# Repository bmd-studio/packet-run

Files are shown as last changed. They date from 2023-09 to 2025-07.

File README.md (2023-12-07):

Packet Run
<br /> <br />
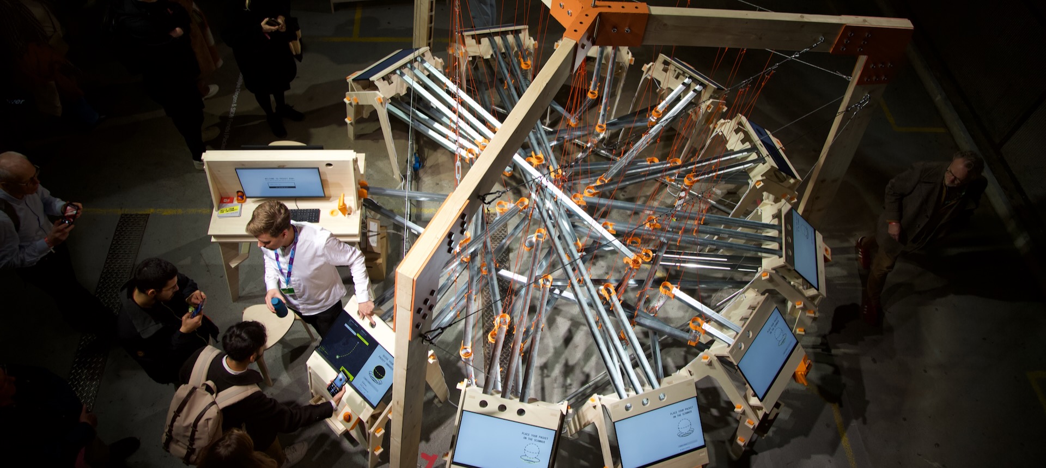
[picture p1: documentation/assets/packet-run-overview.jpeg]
Packet Run overview

<br />

Packet Run is an interactive art installation that visualises how data travels
across the internet in discrete packets. This process is known as **Internet
Protocol routing**.

Packet Run aims to clarify the hidden process of packet routing, thereby showing
everyday users what this process looks like, what risks are involved in the
process and what the future of the internet could look like.

Packet Run has been exhibited at the **2023 Dutch Design Week**,
October 21-29 2023. Afterwards, Packet Run is available for exhibition at
festivals, conferences and cultural institutions. 

For questions and inquiries, please get in touch with [Lei
Nelissen](https://leinelissen.com).

## Repository

This repository aims to contain all software, hardware, designs and other pieces
that are used to construct Packet Run and to make it tick. 

This repository is split out into a couple different directories that track
various assets, bits and pieces:
* `./client`: Contains all software that is run directly on the terminal units
* `./designs`: Contains various designs, ranging from logos, designed copy to
  STL files for the CNCed and 3D-printed parts of the installation. 
* `./documentation`: Contains documentation for how the installation is built,
  compiled and operated. Find here, for instance:
  * [The architectural diagram for Packet Run](./documentation/architecture.md)
  * [The project planning until the 2023 DDW](./documentation/planning.md)
* `./server`: Contains all software that is run on the server

## Contributors
Bureau Moeilijke Dingen

Packet Run was designed and built by **Bureau Moeilijke Dingen**, an Eindhoven-based
design studio that stimulates self-expression and autonomy through technology.

These people from Bureau Moeilijke Dingen contributed to Packet Run:
* Tijs Duel (3D Design, Mechanical Engineering)
* Jort Band (Technology, Management)
* Eva van der Born (UI/UX, Mechanical Engineering, Construction)
* Joep Elderman (Mechanical Engineering, Construction)
* Bart van Dijk (3D Design, Mechincal Engineering)
* Nils Hollestelle (Graphical Design, Construction)
* Lei Nelissen (Design, Project Management, Technology)

<br />

SIDN

Packet Run was based on [PathVis](https://github.com/SIDN/pathvis), an open
source tool that visualises traceroutes. PathVis was built by **SIDN Labs**, an
experimental group at the .NL domain registry focusing on experimental
technology at the core of the internet.

These people from SIDN Labs contributed to PathVis and Packet Run:
* Elmer Lastdrager
* Ralph Koning
* Caspar Schutijser
* Jelte Jansen

<br />

SIDN Fonds

Building Packet Run was made possible by a grant from **SIDN Fonds**, a public
fund that supports and strengthens the internet and its users. 

## Mentions & Media
After being exhibited at the 2023 Dutch Design Week, some media has picked up on
Packet Run. This is an (incomplete) collection of such mentions. Do note that
some (most) links are in Dutch.

- [Vint Cerf mentions Packet Run](https://elists.isoc.org/pipermail/internet-history/2023-November/009107.html)
- [Nemo Kennislink: Het internet als knikkerbaan](https://www.nemokennislink.nl/publicaties/het-internet-als-knikkerbaan/)
- [Studio 040: Opbouw Dutch Design Week in volle gang (video)](https://studio040.nl/nieuws/artikel/opbouw-dutch-design-week-in-volle-gang-ik-denk-dat-wij-voor-iedereen-hier-iets-te-bieden-hebben)
- [Telegraaf: Van dickpic booth tot volgelhuis uit riool...](https://www.telegraaf.nl/entertainment/804337822/van-dickpic-booth-tot-vogelhuis-uit-riool-waar-kijk-ik-naar-klinkt-massaal-tijdens-dutch-design-week)
- [SIDN: Packet Run is an interactive marble run...](https://www.sidn.nl/en/news-and-blogs/packet-run-is-an-interactive-marble-run-that-shows-people-how-the-internet-works)

## Video
Some recording were made at the Dtuch Design Week, so you can get an impression
of what Packet Run is like.

Packet Run Video on YouTube (https://www.youtube.com/watch?v=9uIs0sh4iYU)
<br />

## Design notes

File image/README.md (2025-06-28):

# Packet Run Image Generation

This directory contains the configuration and scripts for generating the Packet Run Raspberry Pi image using `rpi-image-gen`.

1. Install Podman (Desktop) if not already installed

## Building Images

### Client Image

To build the client image:

```bash
podman compose run build-client-image
```

### Server Image

To build the server image:

```bash
podman compose run build-server-image
```

The generated images will be available in the `deploy` directory.

## Configuration

### Layers

The image is built using layers defined in YAML files:

- `base.yaml`: Common setup including:
  - Node.js repository configuration
  - Tailscale repository configuration
  - Service templates
  - Base packages

- `client.yml`: Client-specific configuration:
  - Kiosk service setup
  - Hall sensor server setup
  - Client-specific packages

- `server.yml`: Server-specific configuration:
  - Server service setup
  - Server-specific packages

### Profile

The `packet-run-client` profile defines the order of layers to apply:
1. Base Debian system
2. Raspberry Pi specific layers
3. Packet Run base layer
4. Packet Run client layer

### Configuration File

The main configuration file `packet-run-client.cfg` includes:
- Base Debian configuration
- Profile selection
- Build options

## Development

To modify the image:
1. Edit the appropriate layer file in `config/meta/packet-run/`
2. Update the profile if adding new layers
3. Rebuild the image using the commands above

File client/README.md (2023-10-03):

# Packet Run — Client
This directory shall contain all software and documentation for running directly on terminal
units. Terminal units contain Raspberry Pi 4 boards.

## GPIO Pins
All terminals contain a [PN532-based NFC scanner board](https://www.tinytronics.nl/shop/nl/communicatie-en-signalen/draadloos/rfid/rfid-nfc-kit-pn532-met-s50-kaart-en-s50-key-tag). Some terminal units may
additionally contain a [3144 Hall Effect
sensor](https://www.tinytronics.nl/shop/nl/sensoren/magnetisch-veld/3144-hall-effect-switch).
Both pieces of electronics are to be connected to the Raspberry Pi GPIO pins, so
that the software can read them.

For reference on how the GPIO pins are numbered, use https://pinout.xyz.

### NFC Reader
The NFC scanner is read using WebSerial. This means that the board should be
connected as a UART device, so it is available over WebSerial. First of all,
make sure the DIP switches on the board are both set to OFF (towards the
numbers). This configures the PN532 in UART/HSU mode. When connecting the pins,
use the pin naming that is bound on the bottom of the board (GND/VCC/TXD/RXD).

The pins should be connected as such (board => RPI):
* GND => GND (pin 6)
* VCC => 5V (pin 4)
* SDA/TXD => UART 1 RX (pin 10)
* SCL/RXD => UART 1 TX (pin 8)

### Hall effect sensor
The hall effect sensor is read through a NodeJS webserver, the code for which
can be found in `./hall-sensor-server`.

Use a ribbon cable to connect the hall sensor to the Raspberry Pi. The following
pin layout connects the pins on the sensor from left to right when the side with
the serial number is facing you.

The pins should be connected as such (sensor => RPI):
* SUPPLY (left) => 5V (pin 2)
* GROUND (middle) => GND (pin 9)
* OUTPUT (right) => GPIO 2 (pin 3)

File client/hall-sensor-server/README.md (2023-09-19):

# Packet Run — Hall Sensor Server
This is a Node script that will output the value of a particular GPIO Pin (#2)
as a simple text-based API whether the magnet is engaged or not.

The API is server on `http://localhost:8000` and will output a simple `true` or
`false` for all routes. `true` means a magnet is close to the hall sensor,
`false` means a magnet is absent.

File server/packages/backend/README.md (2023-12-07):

# Packet Run — Back-end
This package contains the back-end code for Packet Run. It's a NestJS-based Node
back-end that is almost exclusively accessed through its GraphQL-based API,
powered by Apollo Server. It features a Worker Queue powered by BullMQ.

## Requirements
This package requires a relatively recent version of NodeJS (v20+
recommended). You will also need redis (v7+ recommended) for the event queue.

## Usage
1. In order to start the front-end, first install all NPM packages:
```
npm install
```

2. Then, create a `.env` file from the default example:
```
cp .env.example .env
```

3. (OPTIONAL) Set your [IPRegistry API
   Token](https://dashboard.ipregistry.co/keys) in the the `.env` file. If you
   don't set it, no IP metadata will be displayed.

4. Run all migrations
```
npm run initialize
```

5. Start the development server
```
npm run dev
```

The back-end is served by default on port `8080`. You may interact with it
through GraphQL (available on `http://localhost:8080/graphql`).

## Architecture
This codebase is split out into a number of modules, services and providers that
together create the full back-end service. You can find an overview of all
modules that are loaded in this application at `./src/app.module.ts`.

### Databasae
The back-end is powered by an SQLite database that is stored locally. By running
`npm run initialize`, this database is initialised, migrated and seeded. The
database is located in the `./data/packet-run.db` file.

The database is accessed through the MikroORM ORM layer. This layer features a
number of `entities` (or "models") that are stored in
`./src/entities/**/index.entity.ts`. Each files corresponds with a table in the
database, and the files contain the properties that should be available in the
database, along with their types.

The database is automagically migrated through the [MikroORM migration
manager](https://mikro-orm.io/docs/migrations). Whenever entity files are
changed, it's recommended to generate a new migration.

MikroORM also features subscribers, which allow create/update hooks for all
models. These are co-located with the entitities in `./src/entities/**/subscriber.ts`.

### GraphQL
The data is made available through an GraphQL API. In order to specify data
access for these, you can find resolvers (in `./src/entities/**/resolver.ts`)
that specify which models are available in the API and how they should exactly
be resolved. The output types for the GraphQL API are defined as GraphQL
"models" in `./src/entities/**/model.ts`.

These resolvers also specify which mutations should be made available to
clients, and how they should be handled. 

In order for the application to respond as quickly as possible to user inputs,
the back-end makes most of it data available across WebSockets, actively pushing
data to clients whenever models are updated. There is some glue code that hooks
into the MikroORM subscribers that automatically triggers GraphQL updates
whenever entities are changed.

### Jobs
We use traceroute to gather the route to a particular website. As traceroute is
asynchronous, we need to perform some tasks asychronously, as new addressed come
in. In order to facilitate this, we use a BullMQ queue, with jobs that are
defined in `./src/jobs`.

These jobs include traceroute itself, retrieving IP metadata from IPRegistry, as
well as retrieving the website and exporting it as an image so we display it
later. The latter task is accomplished in a headless Chrome instance powered by
Puppeteer.

As the BullMQ queue is powered by redis, you will need to have redis installed
locally. Note that the current back-end implementation assumes your redis client
is unauthenticated.

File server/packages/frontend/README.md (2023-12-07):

# Packet Run — Front-end
This package contains the front-end for Packet Run. It's a React-based frontend
powered by [NextJS](https://nextjs.org). It features Apollo for data fetching,
Styled Components for styling and mapbox-gl for map rendering.

## Requirements
This package requires a relatively recent version of NodeJS (v20+
recommended). 

## Usage
1. In order to start the front-end, first install all NPM packages:
```
npm install
```

2. Then, create a `.env` file from the default example:
```
cp .env.example .env
```

3. (OPTIONAL) Set your [Mapbox API
   Token](https://account.mapbox.com/access-tokens/) in the `.env` file. If you
   don't maps will not work

4. Start the development server
```
npm run dev
```

Follow the link provided in your CLI and the application should be work. This
codebase assumes the back-end will be running on the same host on port `8080`.
Please refer to the [back-end documentation](../backend/) for information on
setting up the back-end.

A dashboard is available on the root route (http://localhost:3000/) that
displays the back-end status for the full system.

## Architecture
This codebase is structured so that the Raspberry Pi clients connect to the
back-end through a URL that is formatted according to their id (e.g.
`http://localhost:3000/terminal/8`). Depending on the terminal type, they are redirected
to their respective pages (e.g. `http://localhost:3000/router/8`). These various
pages handle functionalities specific to their terminal type. 

In these pages, the front-end will make a connection to the back-end over
Websockets. Any time an update is issued, all data is updated and the page
re-renders. The philosophy for this codebase is that any and all changes are
send to the back-end, after which the back-end updates its data, updates are
sent over websocket the front-end and the front-end re-renders. As little data
is stored on-client as possible to mitigate risks of crashes.

The front-end attempts to connect to required peripherals, such as NFC readers
(connected via WebSerial) or Hall Sensors (connected over the [HTTP API hosted
by the client](../../../client/hall-sensor-server/)). The logic for these
connections is abstracted using the hooks in the `./src/lib` directory.

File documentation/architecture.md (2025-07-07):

# DDW2023 Software Architecture

## System diagram

```mermaid
flowchart LR
    subgraph server["Server (Raspberry Pi)"]
        subgraph workers["Workers"]
            hop-worker("Worker (mtr / traceroute)")
            website-worker("Worker (website)")
            ip-worker("Worker (IP Geolocate + WHOIS)")
        end

        frontend("Frontend (NextJS)")
        backend("NestJS (GraphQL)")
        websockets("Websockets")
        db("Database (SQLite)")
    end

    subgraph terminals["Terminals (Raspberry Pi x12)"]
        chromium("Interface (Chromium)")
        nfc-reader("NFC Reader (PN532)")
        config-server("Static Config Server (Caddy)")
        potentiometer("Potentiometer (optional)")
        pot-reader("Potentiometer reader script")
    end

    subgraph internal-routing["Internal Routing"]
        switch("Switch")
    end

    subgraph external-routing["External Routing"]
        internet("Internet (WiFi / Ethernet)")
    end

    internet <--HTTPS--> website-worker
    internet <--ICMP--> hop-worker
    internet <--HTTPS--> ip-worker
    internet <--WHOIS--> ip-worker

    backend <--IPC--> hop-worker
    backend <--IPC--> website-worker
    backend <--IPC--> website-worker
    backend <--IPC--> db
    backend <--IPC--> websockets

    frontend <--HTTP--> switch
    backend <--HTTP--> switch
    websockets <--WS--> switch

    switch <--HTTP--> chromium
    switch <--WS--> chromium
    chromium <--WebSerial--> nfc-reader
    config-server <--HTTP--> chromium
    config-server <--HTTP--> switch
    potentiometer <--"C(++)"--> pot-reader

    %% Could also connect to back-end instead, storing the state there and
    %% updating the terminal via a seperate WS connection
    pot-reader <--"WebMIDI / WS"--> chromium
```

## Table structure

### Relational

```mermaid

```

### Flat
```ts
/**
 * A single run tracks all data that is required for handling a succesful user
 * journey across the installation.
 */
interface Run {
    /** 
     * Uniquely identifies a full run. 
     * Format: nano-id, 12 characters (e.g. LtDWYYqPXujf) 
     */
    id: string;
    /** 
     * Format: 4- or 7-byte integer, hexadecimally encoded (e.g. 
     * `04 9C 64 D2 45 2B 80`).
     * NOTE: balls / NFC ID's MAY BE re-used, so there are no guarantees that 
     * an NFC ID uniquely identifies a particular request.
     */
    nfcId?: string;
    /**
     * The website the user has requested to route to.
     * Format: URL, including protocol, preferably HTTPS.
     */
    url: string;
    /**
     * The final destination (server) for this run.
     */
    destination: Address;
    /**
     * An ordered list that describes which hops are encountered en route to
     * the destination.
     * Format: array of `Address`es. null indicates that the hop is not responding
     * NOTE: The destination (server address) is NOT a part of the `hops` arrays
     */
    hops: (Address | null)[];
    /** 
     * At which terminal id this run was last seen
     * Format: number (terminal id)
     */
    terminalId: number;
    /** 
     * Describes the route that is taken during the run
     * Format: array of `Address`es and `Terminal`s
     */
    route: {
        address: Address;
        terminalId: number;
    }[];
}

/**
 * An interactive unit that can handle a number of tasks that are associated
 * with routing. Terminals are arranged in a circle, contain a screen, an NFC
 * reader and potentially a mechanism for creating/transforming packets.
 */
interface Terminal {
    /**
     * An unique identifier for a particular terminal. 
     * Format: 1-12 (potentially 1-20, including spares), with reserved numbers:
     * * 1: `sender`
     * * 2: `gateway`
     * * 3-4 + 6-8 + 10-11 : `router`s
     * * 5 + 9 : `server`s
     * * 12: `receiver`
     * * 13-20: spares
     * NOTE: Numbers are assigned radially in clockwise order, starting at the
     * `sender` and ending at the `receiver`.
     * NOTE: In case a terminal dies, a new unit should not receive the id of
     * the unit it replaces. Rather, it should retain its pre-set id, with the
     * `type` adjusted to the terminal it replaces.
     */
    id: number;
    /**
     * The type of the terminal. This determines what capabilities the terminal
     * has, and which tasks it can accomplish.
     * Format: string enum, with distinct values:
     * * `sender`: Creates a request and dispatches it to an `gateweay`
     * * `receiver`: Receives a response and displays it on a connected screen
     * * `server`: Receives a request, transforms it into a response, and 
     * * dispatches it to an `internet-router`
     * * `gateway`: A special type of router that bridges a `sender` and an
     * internet of `router`s
     * * `router`: 
     */
    type: 'sender' | 'receiver' | 'server' | 'gateway' | 'router';
    /**
     * What the terminal is currently doing.
     * Format: string enum, with distinct values:
     * * `idle`: The terminal is active and operational, but not currently in use
     * * `scanning_nfc`: A packet is currently being scanned using the NFC reader
     * * `creating_packet`: A packet is actively being created or transformed on
     * the terminal
     * * `created_packet`: A special version of `scanning_nfc`: the packet has
     * been transformed, but is still actively being scanned.
     * * `offline`: The terminal has failed its heartbeats and is considered offline.
     * TODO: Create a state machine that describes how states transition into each other
     */
    status: 'idle' | 'scanning_nfc' | 'creating_packet' | 'created_packet' | 'offline';
    /**
     * The payload that is associated with the current status for this 
     * terminal. Currently contains the run id when the terminal is actively being used.
     * TODO: Consider other relevant payloads
     */
    payload: string | null;
    /**
     * When the terminal last connected to the back-end.
     * Format: UNIX epoch timestamp
     */
    lastSeenAt: number;
    /**
     * To which other terminals this terminal has an outbound connection.
     * Format: number array[1-4], specifying the terminalId (e.g. `[3, 4, 6, 9]`)
     */
    connections: number[];
}

/**
 * This type describes the metadata that is available for a particular IP address.
 * NOTE: This interface is still unstable and will be replaced in the future.
 * It will most likely be modeled after the https://ipregistry.co API.
 */
interface Address {
    ip: string;
    operator?: string;
    location?: {
        city?: string;
        region?: string;
        country?: string;
        latitude?: number;
        longitude?: number;
    }
    asn?: number;
    /**
     * When this data was last updated.
     * Format: ISO date
     */
    updatedAt: string;
}
```

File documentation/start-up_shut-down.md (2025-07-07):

# D2-Start-up and shutdown guide

## PACKET RUN

This guide will give instructions on how Packet Run should be started at the beginning of a day, and how it should be shutdown at the end of one. When you run into issues, consult the Troubleshooting Guide, which lists common issues and how to resolve them.

## Starting up Packet Run

1. Power the installation.

Connect the power plug from the desk to a power source, probably located in the desk as well. All terminals and the Mac mini should boot automatically.

2. Ensure that all terminals have booted properly.

They should be displaying their regular terminal screen (the grey one).

3. Ensure all NFC scanners are working.

Take a ball, and place them on the scanner for each terminal. The screen should display "Invalid packet detected" when the ball is placed on the scanner.

4. Ensure the installation is working.

Make two full runs throughout the installation to ensure the installation is working as expected.

## Shutting down Packet Run
Remove power from the installation.

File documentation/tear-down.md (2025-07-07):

# D2-Teardown Guide

This guide describes how the Packet Run installation should be torn down. Please refer to the following documents providing information on track layout, required parts, tools and materials.

- [ ] Inventory of Parts
- [ ] Required tools and materials
- [ ] Track list and build order

## Deconstruction

Deconstructing the installation should be done in the following order, as some parts may not be properly accessible until other parts are removed first.

### Removing the desk

Firstly, remove any and all cables that connect the desk to the installation. Remove the ethernet cables from the router (leave them on the ground for now). Also remove both ethernet cables that are directly plugged in to the Mac mini. Store the ethernet cable that has the dongle attached to it in the desk. Remove the power cord that powers the installation from the socket and coil it up on the inside of the desk. Lastly, remove the power cable coming in from terminal 11 from the power socket inside the desk.

Secondly, disconnect both tracks that are attached to the desk. The one under the desk should be freely floating, so you can remove it and put it on the ground for later removal. The outgoing track is bolted to the desk, and you will need to disconnect it in order to remove the desk. Remove the bolts in the track using an M3 Allan wrench. After removing the track, make sure to screw the bolts back in the mount, so that we don't lose them.

Lastly, keep the peripherals in place using painter's tape. This goes particularly for the keyboard. If you see mouse dangling somewhere, store in on the inside of the desk. Also, remove the Mac mini from the inside of the desk, after disconnecting all cables.

That's it. The desk should now be freely movable and can be put to the side. Make sure it is out of the way for now. When moving the desk, take care to lift it using the lower plate of the worktop, as the upper one is not bolted to the rest of the desk.

### Dismantling the tracks

The tracks form an intricate web that is difficult to construct. Hence, please take care following the steps carefully and one-by-one, so that reconstructing the tracks is a feasible task.

Firstly, find the box of numbered pairs of IKEA clips. Then, attach a pair of clips to each rope and the corresponding steel cable it is attached to. Try to attach the clip on the steel cable as close as possible to the position where the rope is attach to the steel cable. Ensure the numbers on the clip are matching and don't disconnect any ropes until all of them have a clip on them.

Afterwards, all tracks should be removed one-by-one. It's best to remove them in the order they were installed in. Refer to the attached Track list and build order for the installation order. Remove the tracks with build order number 3 first, then 2 and lastly 1. For removing a single track, follow the next paragraph. Always remove a track with at least two persons.

The receiving prongs for the slinky are quite brittle. Please take care when removing tracks and bunching them up that they don't break.

Firstly, one by one, remove the ropes from the hooks attached to the steel cables. Bunch up the ropes and put them inside of the track. Ensure that the rope hold is attached to the track. If it is not properly attached, use a piece of painter's tape to make sure it stays in the exact same place when being moved. Leave the hooks hanging on the steel cable for now.

Track segments should never be disconnected. They should be transported as one single piece.

Secondly, manoeuvre the track out of the installation. This might entail making some weird twister moves in order to get it out in a single piece. The start of the track is locked into a terminal by friction fit. You can remove it by lifting the end of the first segment into the air and wiggling the track out.

Thirdly, pack up the tracks segments in a single package using the rope. Make sure that it's safe for transportation, paying special attention to the prongs on the receiving slinky piece. Also, ensure that the tracks are sorted into their respective build order groups.

Rinse and repeat until all tracks are removed from the installation.

### Removing the terminals

As soon as all tracks have been disconnected from the terminals, the terminals can be removed from the installation as well. Before starting to remove individual terminals, cut all tie-wraps connecting ethernet and power cables to the superstructure.

Firstly, remove the white power cords from each power strip. These cords connect the terminal's power through to each other. Coil up the power cord belonging to a terminal and put it on one of the hooks for the outgoing tracks.

Secondly, coil up the ethernet cable going to the terminal, and place it on another hook for one of the incoming tracks. Don't add the coil to the existing coil on the underside of the screen, as the cable lengths have been closely calibrated.

Now that the terminal is fully disconnected, you can remove it from the circle. Terminals should always be transported fully assembled.

### Dismantling the superstructure

The superstructure consists of a centre piece, to which three side beams are connected. At the end of these horizontal beams are side plates, to which vertical beams are attached. The assembly of a sidebeam, a vertical beam and two side plates is called a leg.

The superstructure is heavy and dangerous. It must be assembled / disassembled by a team of at least four people.

Find the wooden attachments for the lifting tripods. Then, position each of three lifting tripods under a horizontal beam, and gently lift them so that they barely lift the superstructure of off the ground.

Secondly, remove all stainless steel cables and support beams. Remove the cables by relaxing the wire strainer and removing the cables from the hooks. Remove the beams by using an Allan key to loosen the center connector piece.

Thirdly, remove one of the legs by loosening the bolts. Take off the leg first, and then remove the plates one-by-one. Rinse and repeat for the two remaining legs until all side plates and vertical beams are removed. Then, lower the remaining assembly using the lifting tripods, as low as they can go. Lift what remains of the superstructure from the lifting tripods and place it on the ground. You can now remove the vertical pieces from the center piece by loosening the bolts and pulling the beam out. 

The superstructure is now fully disassembled and ready for transportation.

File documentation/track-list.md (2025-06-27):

# Packet Run Track List
This page contains all tracks in Packet Run.

Note that the numbering consists of two numbers. The T-prefix denotes the
terminal number for the track (1-12, counterclockwise, starting at desk),
whereas the S-prefix denotes the slot (1-4, left to right as seen from
front-side of terminal). Sending side slots consist of the holes at the top of a
terminal, whereas receiving side slots are on the bottom rear section of there
terminal. 

Each track contains multiple track segments (1-4, counted from sending
side). All track segments are labeled, where the track segment is denoted with a
P-prefix. 

Lastly, tracks are sorted into a build order category (1-3). This
signifies which tracks should be installed first (1), middle (2) and last (3).
During teardown, the build order should be reversed (3 first, 2 middle, 1 last). 

| Sending side | Receiving side | № segments | Build order № |
|---|---|---|---|
| T1-S1 | T2-S1 | 2 | 1 |
| T2-S1 | T12-S1 | 2 | 3 |
| T2-S2 | T6-S2 | 3 | 2 |
| T3-S1 | T11-S3 | 3 | 3 |
| T3-S2 | T8-S1 | 2 | 1 |
| T3-S3 | T6-S1 | 2 | 2 |
| T4-S1 | T11-S2 | 2 | 3 |
| T4-S2 | T7-S1 | 3 | 3 |
| T4-S3 | T5-S1 | 2 | 3 |
| T5-S1 | T2-S4 | 3 | 3 |
| T5-S2 | T4-S3 | 2 | 2 |
| T6-S1 | T3-S3 | 3 | 1 |
| T6-S2 | T2-S2 | 3 | 2 |
| T6-S3 | T10-S3 | 3 | 2 |
| T7-S1 | T4-S2 | 3 | 2 |
| T7-S2 | T10-S2 | 3 | 2 |
| T8-S1 | T3-S2 | 3 | 1 |
| T8-S2 | T11-S1 | 3 | 2 |
| T9-S1 | T2-S3 | 2 | 1 |
| T9-S2 | T10-S1 | 2 | 3 |
| T10-S1 | T9-S1 | 2 | 3 |
| T10-S2 | T7-S2 | 3 | 3 |
| T10-S3 | T6-S3 | 4 | 3 |
| T11-S1 | T8-S2 | 2 | 2 |
| T11-S2 | T4-S1 | 3 | 3 |
| T11-S3 | T3-S1 | 3 | 3 |

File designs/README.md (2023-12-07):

# Packet Run — Design
This directory shall contain all designed elements that are made in connection
with Packet Run, whether they're visual designs, mechnical designs or 3D
designs.

NOTE: Git is our version management. Overwrite previous files with newer
versions, rather than adding them under a new filename.

# Uploading and Review
All designs need to be reviewed by Tijs.
- Make sure all sketches are 'locked'
- Make sure that multipart/multi-body are split in seperate files _and_ there is an assembly file.

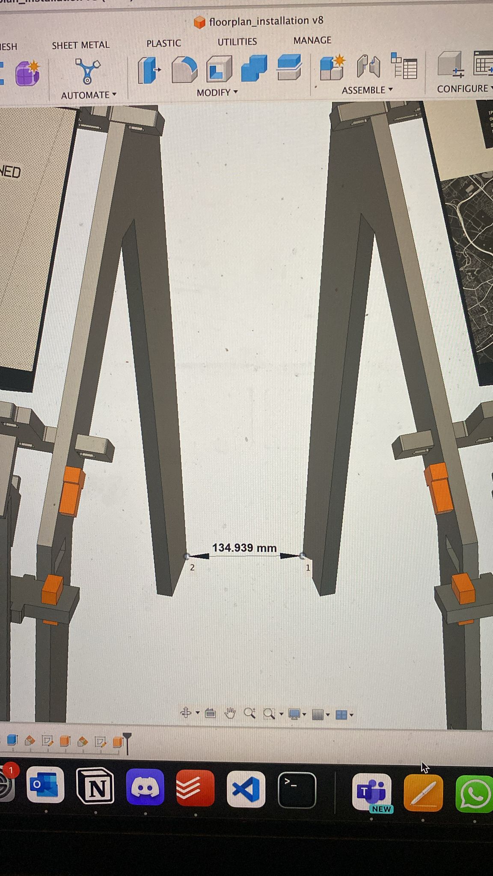
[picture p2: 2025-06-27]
documentation/assets/terminal-spacing.jpeg

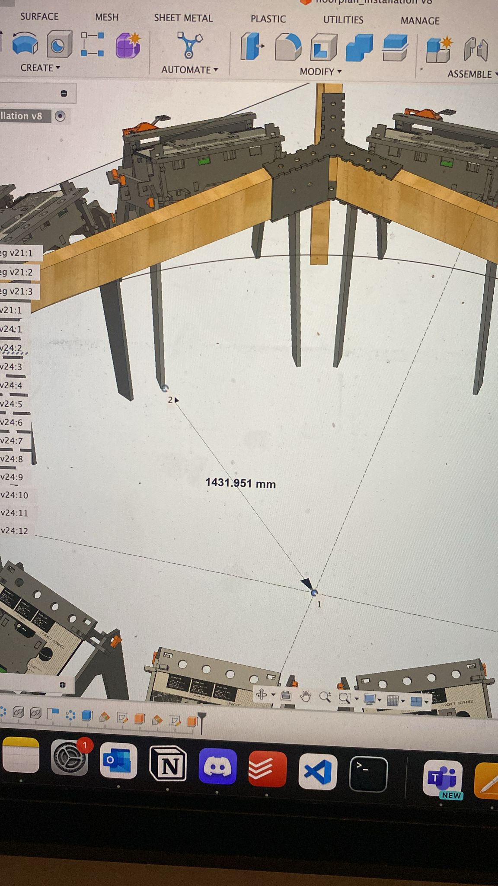
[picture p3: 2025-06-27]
documentation/assets/terminal-distance-to-center.jpeg

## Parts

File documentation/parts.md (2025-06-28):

# Packet Run Parts

This list contains all parts belonging to Packet Run. They should be checked before transporting everything for assembly at location, as well
as when retuning the installation.

All parts fit in a 2m x 3,85m truck bed.

## Terminals
- [ ] 8x regular plywood terminal unit (labeled), consisting of:
    - [ ] 1x Raspberry Pi
    - [ ] 1x 24” monitor
    - [ ] 1x Power strip
    - [ ] 1x Ethernet cable
    - [ ] 1x NFC scanner, connected to Raspberry Pi GPIO Pins
    - [ ] 1x wooden top assembly
    - [ ] 1x wooden bottom assembly
    - [ ] 2x legs (marked L and R on bottom)
    - [ ] 1x ball receiving tray
- [ ] 2x plywood terminal unit with press, labeled
- [ ] 1x box of SD cards
- [ ] 1x box of M3x16 Torx screws

## Desk
The desk is a single unit that consists of these parts:
- [ ] 2x integrated terminals, each consisting of
    - [ ] 1x Raspberry Pi + USB-C power brick
    - [ ] 1x 24” HDMI Monitor + Power brick
    - [ ] 1x NFC assembly, connected to Raspberry Pi GPIO Pins
    - [ ] 1x Press assembly with hall sensor, connected to Raspberry Pi GPIO Pins (only for sender side)
    - [ ] 1x Ethernet cable, routed through bottom opening to switch
    - [ ] 1x Keyboard
- [ ] 1x server:
    - [ ] 1x Raspberry Pi + USB-C power brick
    - [ ] 1x USB-C Ethernet dongle, connected to switch
- [ ] 1x Power socket
- [ ] 1x Ethernet switch, with power cable
- [ ] 1x KVM switch for switching between terminal 1 and server, including:
    - [ ] 3x HDMI Cable (2x input, 1x output)
    - [ ] 1x Keyboard
    - [ ] 2x USB host cable
    - [ ] 1x micro-USB switch, for toggling between connected computers
- [ ] 1x 10m Ethernet cable, with Ethernet coupling piece

Additionally, the following peripherals should be packed with the desk:
- [ ] 2x wooden stool
- [ ] 1x banner with wooden housing
- [ ] 500x flyers
- [ ] 500x postcards
- [ ] 150x ball, in box

## Tracks
- [ ] 26x track set, labeled (see [track list](./track-list.md)), grouped in three sets (build order 1-3), each containing:
    - [ ] 1-2x rope holds per segment, taped in place with painter’s tape
    - [ ] 1x rope per rope hold
    - [ ] 1-3x slinky assembly connecting track segments

## Superstructure
- [ ] 3x horizontal wooden beam, labeled H1-H3
- [ ] 3x vertical wooden beam, labeled V1-V3, with attachment points for steel cables and support beams
- [ ] 1x steel center piece
- [ ] 6x steel side plates, labeled C1-C6
- [ ] 6x steel scaffolding beams, labeled SC1-SC6
- [ ] 3x scaffolding connector unit with dual hex sockets, labeled SS1-SS3
- [ ] 3x 2m stainless steel cable with carabiner and wire strainer, labeled W3-1 - W3-3
- [ ] 3x 3m stainless steel cable with carabiner and wire strainer, labeled W2-1 - W2-3
- [ ] 6x 2.5m stainless steel cable with carabiner and wire strainer, labeled W1-1 - W1-3
- [ ] Box of 100x IKEA stainless steel S-ring
- [ ] ~48x M18 bolts and nuts
- [ ] 1x M22 eye nut, preferably fastened to the top of the center piece
- [ ] 6x boxes containing clips (white, IKEA)
- [ ] Spare parts

To suit varying circumstances, especially during construction, it might be
wise to bring some spare parts along. The following parts and amounts are
recommended:
- [ ] 6x slinky receiver
- [ ] 6x slinky sender
- [ ] 6x rope hold including rope
- [ ] 6x T-piece
- [ ] 6x track end-stop
- [ ] 1x Hall sensor assembly
- [ ] 1x NFC scanner, including wires
- [ ] 1x Raspberry Pi

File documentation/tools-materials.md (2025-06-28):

# Packet Run Tools & Materials
This is a list of tools and materials that are needed to both build up and tear
down Packet Run. The materials are mostly needed for buildup.

## Required tools
### Lifting
- [ ] 1x support rod (bouwstempel)
- [ ] 3x lifting tripod (takelstatief): Manfrotto 087
- [ ] 3x U-shape lifting attachments
- [ ] 2x stepladder
- [ ] 1x (laser) level

### Tools
- [ ] 2x M22 spanner (moersleutel)
- [ ] 2x Adjustable spanner (Engelse sleutel)
- [ ] 1x M6 Allan wrench (inbussleutel)
- [ ] 1x M3 Allan wrench (inbussleutel)
- [ ] 1x M3 Torx screwdriver
- [ ] 3x cutting plier (kniptang)
- [ ] 2x measuring tape
- [ ] 1x rubber hammer
- [ ] 1x steel hammer
- [ ] 1x lighter

### Miscellaneous
- [ ] 3x large storage box
- [ ] 3x full roll of painter’s tape
- [ ] 1x 25m cable reel
- [ ] 1x USB-A keyboard (for debugging)
- [ ] 12x spanbanden

## Required materials
- [ ] 100x small black tie-wrap
- [ ] 100x large black tie-wrap
- [ ] Box of M3x8mm hex socket screws
- [ ] Box of M3 lock nuts (borgmoer)

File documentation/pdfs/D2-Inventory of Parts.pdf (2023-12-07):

# Inventory of Parts

This list contains all parts belonging to Packet Run. They should be checked before transporting everything for assembly at location, as well as when retuning the installation.

All parts fit in a 2m x 3,85m truck bed.

Terminals

Desk

The desk is a single unit that consists of these parts:

Exposition ______________________________ | Date ____ / _____ / ___________

8x regular plywood terminal unit (labeled), consisting of:

1x Raspberry Pi

1x 24” monitor

1x Power strip

1x Ethernet cable

1x NFC scanner, connected to Raspberry Pi GPIO Pins

2x plywood terminal unit with press, labeled

1x rope measure for terminals

1x template for measuring terminal spacing

1x box of SD cards

1x box of M3x16 Torx screws

2x integrated terminals, each consisting of

1x Raspberry Pi + USB-C power brick

1x 24” HDMI Monitor + Power brick

1x NFC assembly, connected to Raspberry Pi GPIO Pins

1x Press assembly with hall sensor, connected to Raspberry Pi GPIO Pins (only for sender side)

1x Ethernet cable, routed through bottom opening to switch

1x Keyboard

1x Mac mini, with:

1x Power cable

1x USB-C Ethernet dongle, connected to switch

1x Power socket

1x Ethernet switch, with power cable

1x KVM switch for switching between terminal 1 and Mac Mini, including:

3x HDMI Cable (2x input, 1x output)

1x Keyboard

1x Mouse

2x USB host cable

Additionally, the following peripherals should be packed with the desk:

Tracks

Superstructure

Spare parts

To suit varying circumstances, especially during construction, it might be wise to bring some spare parts along. The following parts and amounts are recommended:

1x micro-USB switch, for toggling between connected computers

1x 10m Ethernet cable, with Ethernet coupling piece

2x wooden stool

1x Roll-up banner

500x flyers

500x postcards

150x ball, in box

26x track set, labeled (see Track list and build order (https://bmd-studio.atlassian.net/wiki/spaces/D2/pages/2193784833) ), grouped in three sets (build order 1-3), each containing:

2-4x steel track segments

1-2x rope holds per segment, taped in place with painter’s tape

1x rope per rope hold

1-3x slinky assembly connecting track segments

3x horizontal wooden beam, labeled H1-H3

3x vertical wooden beam, labeled V1-V3, with attachment points for steel cables and support beams

1x steel center piece

6x steel side plates, labeled C1-C6

6x steel scaffolding beams, labeled SC1-SC6

3x scaffolding connector unit with dual hex sockets, labeled SS1-SS3

3x 2m stainless steel cable with carabiner and wire strainer, labeled W3-1 - W3-3

3x 3m stainless steel cable with carabiner and wire strainer, labeled W2-1 - W2-3

6x 2.5m stainless steel cable with carabiner and wire strainer, labeled W1-1 - W1-3

Box of 100x IKEA stainless steel S-ring

~48x M18 bolts and nuts

1x M22 eye nut, preferably fastened to the top of the center piece

6x boxes containing clips (white, IKEA)

6x slinky receiver

6x slinky sender

6x rope hold including rope

6x T-piece

6x track end-stop

1x Hall sensor assembly

1x NFC scanner, including wires

1x Raspberry Pi

Version | Date | Comment
Current Version (https://bmd-studio.atlassian.net/wiki/display/D2/viewpage.action?pageId=2197422088) (v. 4) | 16 Oct, 2023 16:55 | Lei Nelissen (https://bmd-studio.atlassian.net/wiki/people/5e907ccfe053b30b7aae6a82?ref=confluence)
v. 3 (https://bmd-studio.atlassian.net/wiki/display/D2/viewpage.action?pageId=2198208598) | 16 Oct, 2023 14:32 | Lei Nelissen (https://bmd-studio.atlassian.net/wiki/people/5e907ccfe053b30b7aae6a82?ref=confluence)
v. 2 (https://bmd-studio.atlassian.net/wiki/display/D2/viewpage.action?pageId=2198110267) | 16 Oct, 2023 11:47 | Lei Nelissen (https://bmd-studio.atlassian.net/wiki/people/5e907ccfe053b30b7aae6a82?ref=confluence)
v. 1 (https://bmd-studio.atlassian.net/wiki/display/D2/viewpage.action?pageId=2197684245) | 16 Oct, 2023 10:11 | Lei Nelissen (https://bmd-studio.atlassian.net/wiki/people/5e907ccfe053b30b7aae6a82?ref=confluence)

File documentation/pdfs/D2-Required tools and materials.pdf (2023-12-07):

# Required tools and materials

This is a list of tools and materials that are needed to both build up and tear down Packet Run. The materials are mostly needed for buildup.

## Required tools

Lifting

Tools

Miscellaneous

Exposition ______________________________ | Date ____ / _____ / ___________

1x support rod (bouwstempel)

2x lifting tripod (takelstatief) + U-shape lifting attachments

2x solid steel rod 18mm (for lifting the superstructure)

2x steel profile (for lifting the superstructure)

1x steel cable that attaches to the profile (for lifting the superstructure)

2x stepladder

1x D-shackle (harpsluiting)

2x M22 spanner (moersleutel)

2x Adjustable spanner (Engelse sleutel)

2x steeksleutel voor steigerbuizen

1x M6 Allan wrench (inbussleutel)

1x M3 Allan wrench (inbussleutel)

1x M3 Torx screwdriver

3x cutting plier (kniptang)

2x measuring tape

1x rubber hammer

1x steel hammer

1x lighter

1x draadeind

2x screwdriver we don’t care about

3x large storage box

1x full roll of painter’s tape

1x 25m cable reel

1x USB-A keyboard (for debugging)

1x trolley for carrying stuffs by old people

3x spanbanden

| Required materials 100x small black tie-wrap 100x large black tie-wrap Box of M3x8mm hex socket screws Box of M3 lock nuts (borgmoer)
Version | Date | Comment

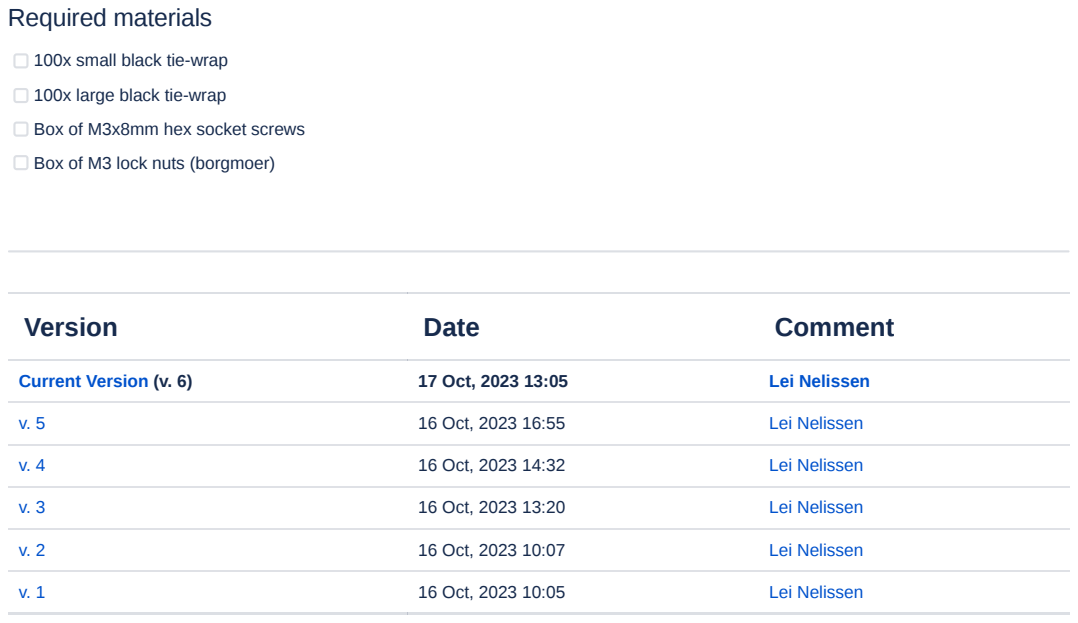
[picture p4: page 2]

Current Version (https://bmd-studio.atlassian.net/wiki/display/D2/viewpage.action?pageId=2197389317) (v. 6) | 17 Oct, 2023 13:05 | Lei Nelissen (https://bmd-studio.atlassian.net/wiki/people/5e907ccfe053b30b7aae6a82?ref=confluence)

v. 5 (https://bmd-studio.atlassian.net/wiki/display/D2/viewpage.action?pageId=2199715841) | 16 Oct, 2023 16:55 | Lei Nelissen (https://bmd-studio.atlassian.net/wiki/people/5e907ccfe053b30b7aae6a82?ref=confluence)

v. 4 (https://bmd-studio.atlassian.net/wiki/display/D2/viewpage.action?pageId=2198208587) | 16 Oct, 2023 14:32 | Lei Nelissen (https://bmd-studio.atlassian.net/wiki/people/5e907ccfe053b30b7aae6a82?ref=confluence)

v. 3 (https://bmd-studio.atlassian.net/wiki/display/D2/viewpage.action?pageId=2198372405) | 16 Oct, 2023 13:20 | Lei Nelissen (https://bmd-studio.atlassian.net/wiki/people/5e907ccfe053b30b7aae6a82?ref=confluence)

v. 2 (https://bmd-studio.atlassian.net/wiki/display/D2/viewpage.action?pageId=2198110212) | 16 Oct, 2023 10:07 | Lei Nelissen (https://bmd-studio.atlassian.net/wiki/people/5e907ccfe053b30b7aae6a82?ref=confluence)

v. 1 (https://bmd-studio.atlassian.net/wiki/display/D2/viewpage.action?pageId=2197553167) | 16 Oct, 2023 10:05 | Lei Nelissen (https://bmd-studio.atlassian.net/wiki/people/5e907ccfe053b30b7aae6a82?ref=confluence)

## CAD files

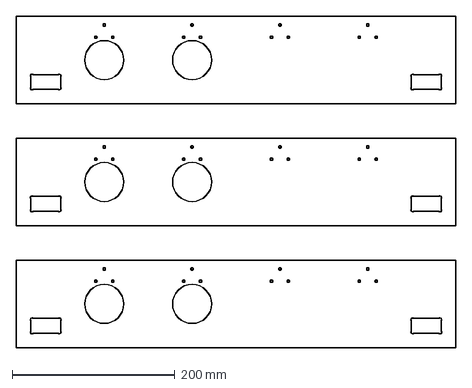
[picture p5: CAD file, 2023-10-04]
designs/dxf/desk/final_parts.dxf
540.0 x 408.0 mm

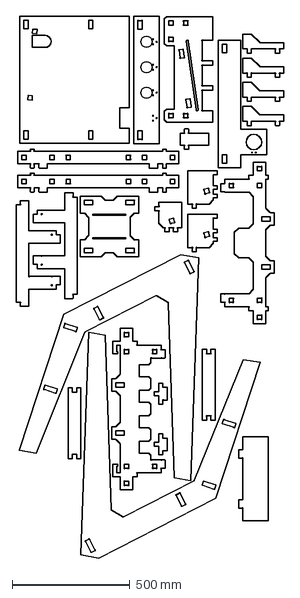
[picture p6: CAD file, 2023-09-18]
designs/dxf/terminal.dxf
1135.3 x 2298.0 mm

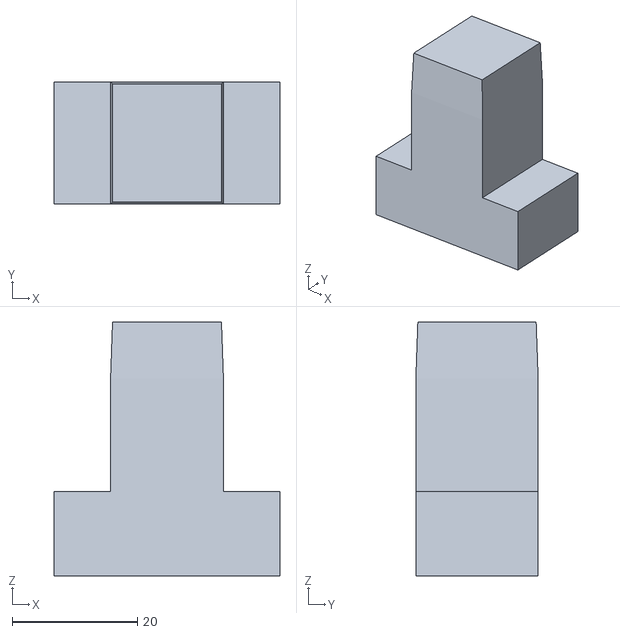
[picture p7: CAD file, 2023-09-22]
designs/stl/alt_pegs/peg_desk_19.50.stl
36.0 x 19.5 x 40.5

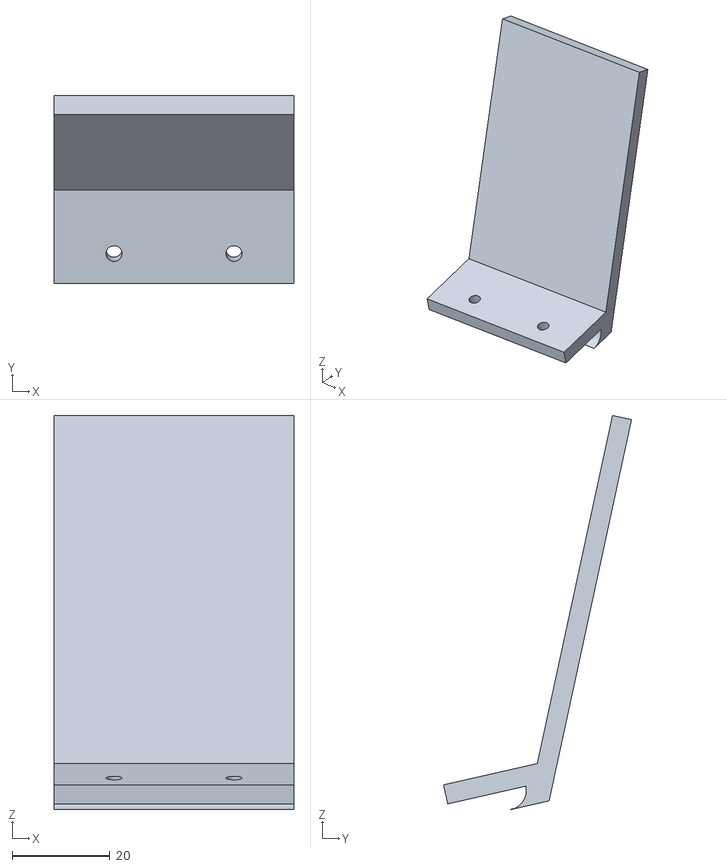
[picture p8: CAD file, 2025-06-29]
designs/stl/desk_dispenser/extension_up_blocker.stl
49.2 x 38.6 x 80.8

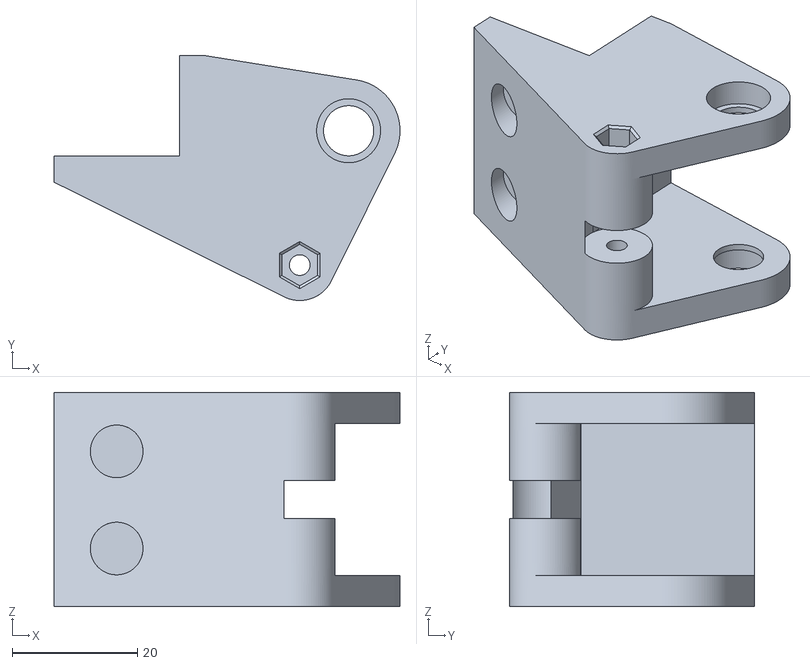
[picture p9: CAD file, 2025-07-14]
designs/stl/grill_hinge_fixed.stl
55.2 x 39.1 x 34.2

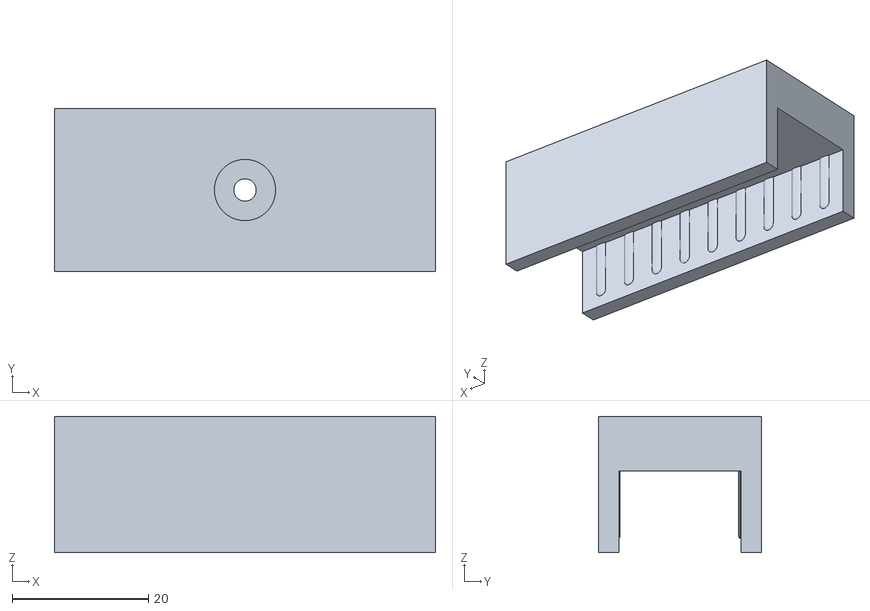
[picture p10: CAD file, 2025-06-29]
designs/stl/track_arrival_clamp/bottom_wood_clamp.stl
56.0 x 24.0 x 20.0

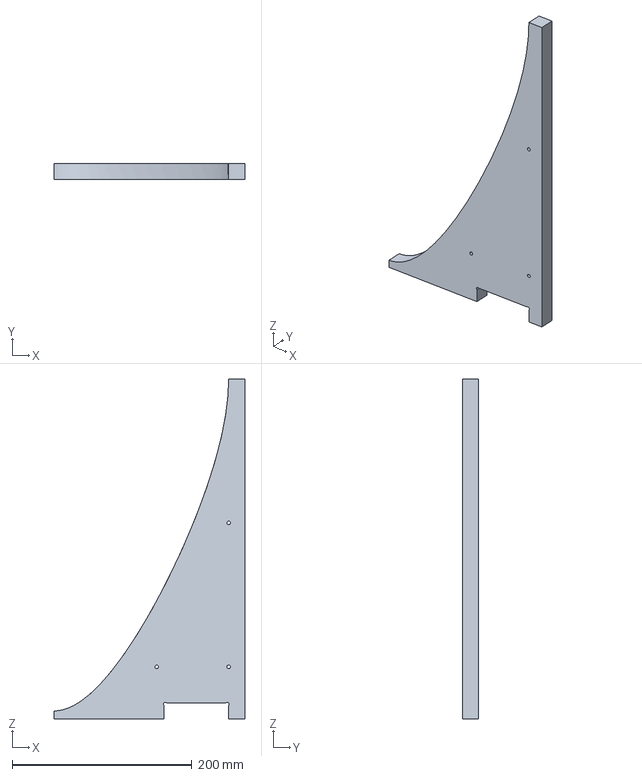
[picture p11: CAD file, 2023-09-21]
designs/dxf/desk/curved_slope v9.step
212.0 x 18.0 x 378.0 mm

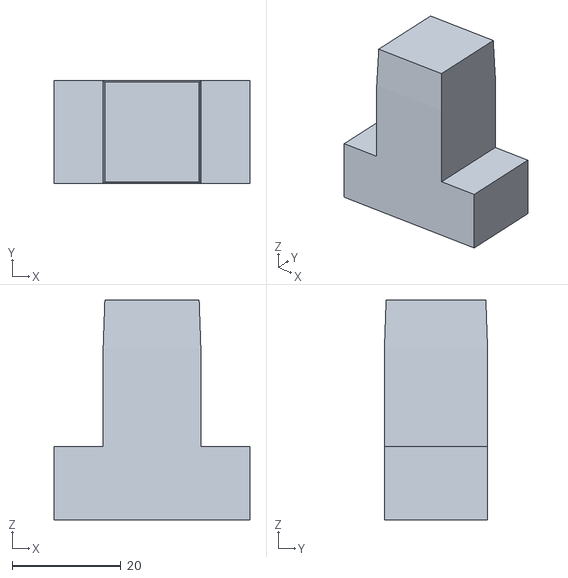
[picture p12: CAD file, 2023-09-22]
designs/stl/alt_pegs/peg_desk_19.00.stl
36.0 x 19.0 x 40.5

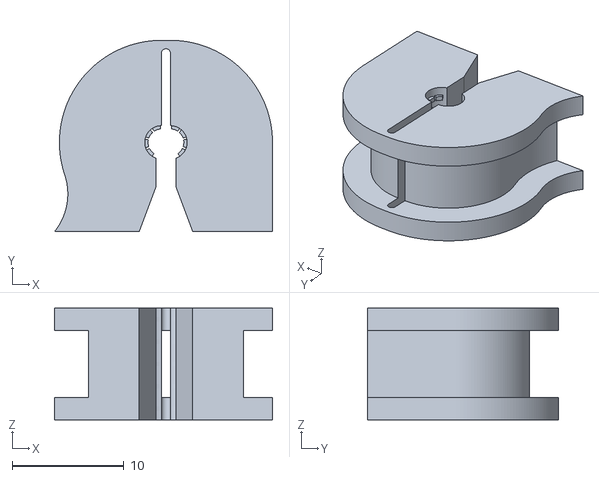
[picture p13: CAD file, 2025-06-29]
designs/stl/cable_clamp.stl
19.5 x 17.1 x 10.0

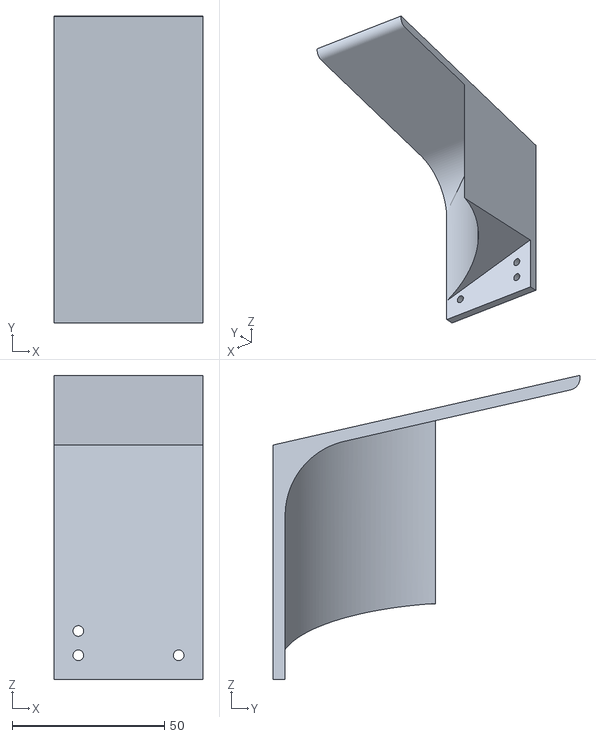
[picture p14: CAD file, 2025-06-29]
designs/stl/desk_dispenser/side_wall.stl
49.0 x 101.0 x 100.1

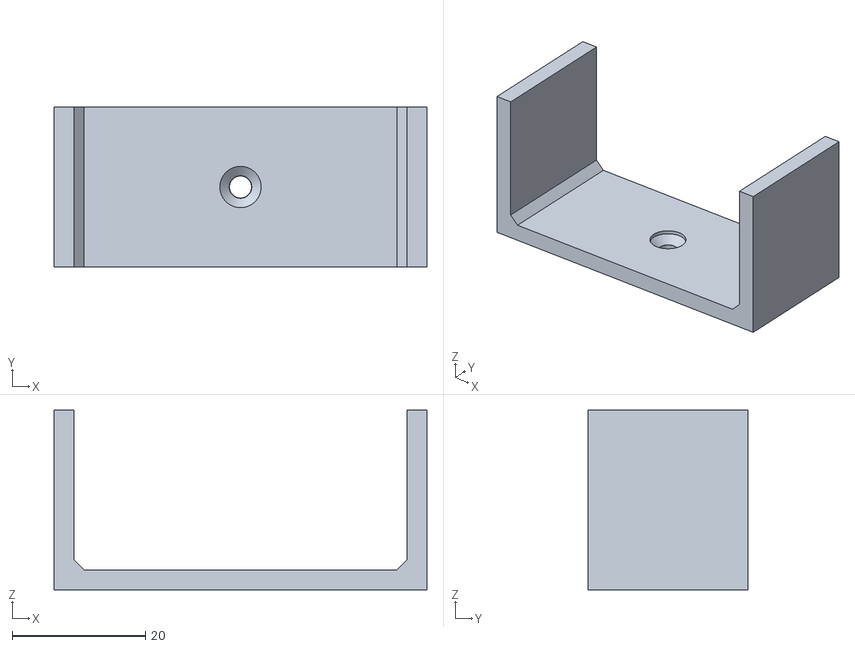
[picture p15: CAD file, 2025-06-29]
designs/stl/track_arrival_clamp/top_track_clamp.stl
56.0 x 24.0 x 27.0

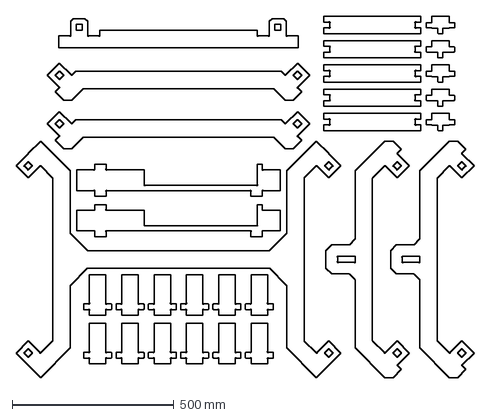
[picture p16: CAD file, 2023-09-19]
designs/dxf/desk/dxf_desk_plate_3.dxf
1416.6 x 1117.9 mm

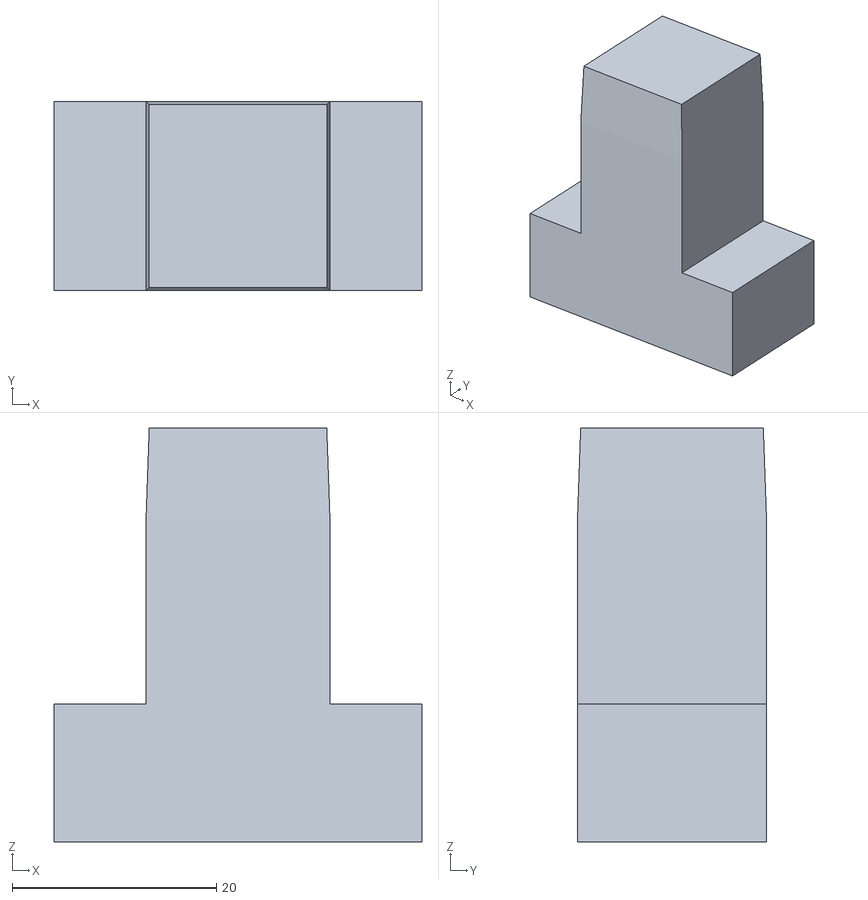
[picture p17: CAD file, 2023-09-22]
designs/stl/alt_pegs/peg_desk_18.50.stl
36.0 x 18.5 x 40.5

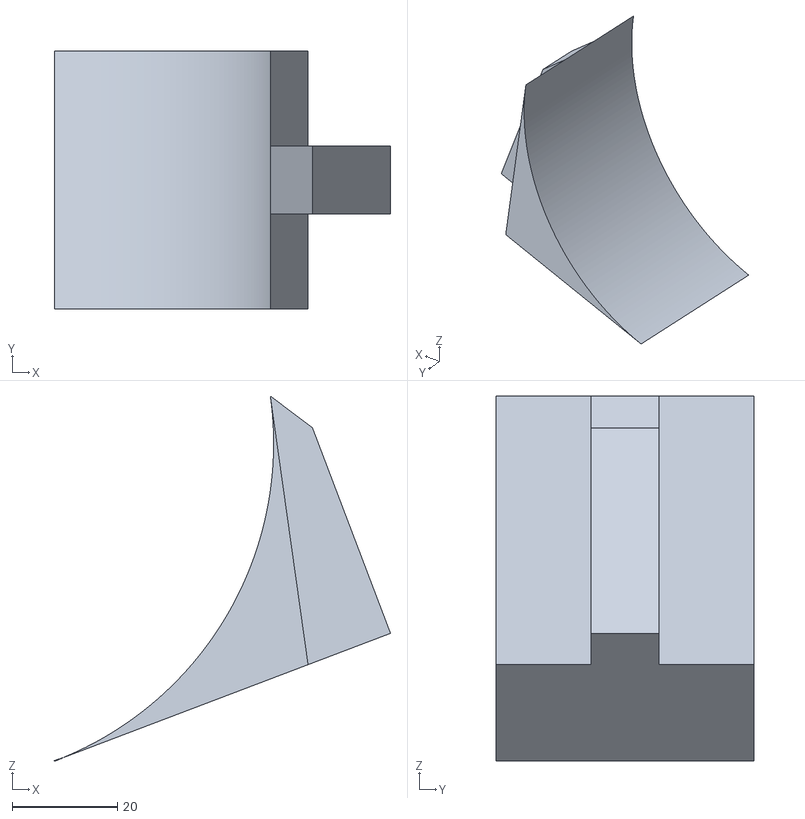
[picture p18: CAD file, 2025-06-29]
designs/stl/desk_dispenser/desk_unblocker_2.stl
63.8 x 49.0 x 69.3

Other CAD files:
designs/stl/terminal_receiving_guide.stl
designs/dxf/desk/dxf_desk_plate_2.dxf
designs/stl/alt_pegs/peg_desk_18.25.stl
designs/stl/desk_dispenser/desk_unblocker_1.stl
designs/dxf/desk/dxf_desk_plate_1.dxf
designs/stl/alt_pegs/peg_desk_18.00.stl
designs/stl/arrival.stl
designs/stl/arrival_desk.stl
designs/stl/cup_scanner.stl
designs/stl/desk_departure.stl
designs/stl/desk_dispenser/bottom_part.stl
designs/stl/desk_leg_bracket.stl
designs/stl/drill_guide_body.stl
designs/stl/drill_guide_lid.stl
designs/stl/drop.stl
designs/stl/grill_handle.stl
designs/stl/grill_hinge_arm.stl
designs/stl/grill_press.stl
designs/stl/hinge_container.stl
designs/stl/hinge_container_cover.stl
designs/stl/nfc_cup.stl
designs/stl/packet_press.stl
designs/stl/peg.stl
designs/stl/rope_hold.stl
designs/stl/scanner_container.stl
designs/stl/scanner_container_conver.stl
designs/stl/terminal_departure.stl
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

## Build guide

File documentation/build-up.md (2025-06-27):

# D2-Build-up Guide

## PACKET RUN

This guide describes how the Packet Run installation should be built up. Please refer to the following documents providing information on track layout, required parts, tools and materials.

- [ ] Inventory of Parts
- [ ] Required tools and materials
- [ ] Track list and build order

## Construction

Constructing the installation requires that the particular order in this document is followed. It's strongly recommended to ensure that all parts are present at location before starting assembly.

## Raising the superstructure

The superstructure consists of a centre piece, to which three side beams are connected. At the end of these horizontal beams are side plates, to which vertical beams are attached. The assembly of a horizontal beam, a vertical beam and two side plates is called a leg. To stiffen the construction, a number of steel cables are attached to hooks in the vertical beams, along with a set of scaffolding beams attached to the base of the vertical beams.

The superstructure is heavy and dangerous. It must be assembled by a team of at least four people. Steel-toed boots are strongly recommended while setting up.

Firstly, ensure that all pieces are present and accounted for. The superstructure should be assembled in one go, in order to ensure stability and minimise any changes of collapse. Make sure to keep anyone out of the build-up area. Before starting the procedure, inform everyone involved exactly how the procedure is carried out. Then, place markers on the floor, indicating rougly where all three legs should end up.

Most parts for the superstructure are numbered (usually 1-3 or 1-6). Numbering in the installation always originates from the desk, halfway between the two legs, following the circle in an anticlockwise manner.

Secondly, place the center piece on the floor, roughly at the center of the exhibition plot. Ensure that the eye nut is safely attached to thread that extends from the top of the center piece. Then, according to the labels, insert the horizontal beams into the center piece, and fasten them with the corresponding bolts.

Thirdly, unfold and place the two lifting tripods next to the center piece so that they're stable. Place the U-shape attachments on top of the tripods. Wrap the steel cable used for lifting the center piece around the steel profiles, and then place the steel profile into the U-shaped attachments.

Fourthly, lift the horizontal assembly off of the ground. Before you lift, ensure that the steel cable is short enough, so that the tripods can fully extend to the working height of the superstructure. This means the assembly might need to be lifted by hand so that it can attach to the steel cable. If you must lift by hand, put one person at the end of each horizontal beam, and a single person at the center. Coordinate so that the assembly is lifted synchronously, and attach it to the lifting tripods. Lift to the full height for the superstructure, approximately 2 m.

Now, all legs shall be added to the assembly one by one. For this, follow these instructions until all legs are safely in place.

Firstly, place a support rod under the end of the horizontal beam you will be attaching the vertical beam to. One person must monitor and hold the beam at all times. Then, using a ladder, attach the side plates, one by one to the vertical beam. Attach the bolts but do not tighten them so the plates remain in place. Subsequently, lift the vertical beam in place, and attach it to the assembly using bolts. Ensure that the beams and plates are oriented well, and then tighten all bolts fully. Lastly, slowly and carefully, remove the support rod from under the leg, checking that it can support its own weight.

Wires are numbered W1 - W3, with W1 starting at the bottom, W2 at the middle and W3 at the top.

Repeat these instructions so that all legs are attached. Finally, the superstructure should be freely standing and mostly stable. If so, remove all lifting equipment from under the superstructure and out of the way. Now, attach all steel cables to the superstructure. Also, attach the scaffolding to the bottom of the vertical beams. Use the sleeves to connect two individual scaffolding tubes into one. Lastly, tighten all wire strainers so that the entire superstructure is in tension.

Before continuing, firstly ensure that the superstructure is in proper tension by wobbling one of the legs. If not, tighten the wire strainers more and ensure all bolts are properly tightened. When you are convinced the superstructure is stable, move the superstructure to its final position.

## Placing the desk

Now that the superstructure is in place, use it to align the desk into place. It should be located -20 cm from the scaffolding tube. It should be perfectly perpendicular to the scaffolding, located in the exact middle of the scaffolding assembly.

Place the Mac mini inside the desk, with the front facing the wooden side panel. Align it using the brown markers on the inside of the desk. Attach the power cable, the USB cable and the Ethernet USB-C dongle that should be nearby.

If already available, route both power and ethernet to the desk. The power cord should be connected to the power strip inside of the desk. Ethernet should be connected to the ethernet port of the Mac mini. Remove any painter's tape keeping any keyboards in place.

Leave the desk for now. More things will be attached to the desk as soon as the terminals are placed.

## Placing the terminals

Next, all terminals should be placed at their appropriate spots. Please refer to an overview of terminal placement as a helpful guide. Terminals are numbered 1-12, and are ordered counter-clockwise in a circle, starting at the desk (terminal 1+12). We recommend using both the placement measuring rope and terminal placement template as follows. To set up the placement measuring rope, place the measuring tape rope through the O-ring in the steel center. Pull it far enough along so that the two ends meet up. Keep them next to each other, in the same direction, and use a piece of tape to secure them to each other. The ends of the rope indicate the position op the back legs for all terminals.

Identify the correct location for a single terminal. Place it in roughly the right space. Then, use the measurement rope to put the terminals at the right distance from the center. The back legs of the terminals should be positioned exactly against the place where the rope meets the ground when at tension. Then, use the placement template to position the terminal relative to the previous terminal. The back legs of the terminal should fit precisely in the template so that the distance between them is equal between all terminals in the circle.

Repeat this process until all terminals are in the right place. Then, run another round with both the template and measuring rope so that all terminals are definitively in the right place. Lastly, put some tape on the ground for each terminal, as to indicate it's desired position.

Now that all terminals are in place, we must connect all cables. First, we'll install the power cables. Starting at terminal 1, take the power cord from the terminal and connect it to power strip of the terminal on its right. Route the cable through the cables guides in both the origin and destination terminal. The cable should be routed down, somewhat across the ground to the next terminal. Repeat this process until all cords are connected. The power cord for terminal 11 should be routed to the desk, and connected to the power strip in the desk.

Next up, install all ethernet cables. Note that there are two coils of cable connected to the terminal, one next to the Raspberry Pi, and another in the departing lanes for tracks. Make sure to leave the coil next to the Raspberry Pi in place, and only uncoil the one in the departing lanes, as all ethernet cables have been approximately measured to order.

To connect a single terminal cable, uncoil the coil the departing lane cable fully. Make sure the cable is mounted through the cable guide, then route it down the leg, under the scaffolding tube. Then, place it on the ground along the scaffolding tubes, taking the shortest routes along the tubes towards the ethernet switch. Make sure to always route the cable along the underside of the scaffolding, so we don't accidentally wrap around or across any tubing or other cables. When arriving at the switch, plug the cable into the port with the number of the terminal.

Now, connect the desk to a wall socket. All terminals should boot. Verify that all terminals are powered by checking the screen lights up and Raspberry Pi boots. Note that the installation won't work until the Mac mini is booted, it's just necessary to verify it is powered right now. Also, verify that all Raspberry Pis have a working ethernet connection, by checking that the corresponding port for a terminal lights up on the ethernet switch. When all checks are complete, power down the installation by pulling the power plug.

The switch might have a bad port that does not work: port 4. If the cable does work in other port, preferably connect it to a port that is the original terminal number +10, or else, any working port.

Lastly, connect the ethernet cable providing internet, and route it along the scaffolding tubes and installation to the Mac mini, connecting the cable to the Mac mini's ethernet port.

When all ethernet cables and power cables are connected, cable manage both along the scaffolding tubes. Neatly order all cables respective to each other, then, use tie wraps to tie cables to the back of the scaffolding tube, approximately every 20-30cm. At the ethernet switch, use tie wraps every 10 cm to tie the cables to each other on the stretch of free-hanging cables between the switch and the scaffolding tube.

## Hanging the tracks

Once the superstructure, the desk and all terminals are in place, only hanging the tracks remains. This is a precise task, that shouldn't be rushed. Before you begin, make sure all tracks are present at the location. Also ensure all track are ordered by build group, according to the respective document: Track list and build order. Then, follow these instructions to hang an individual track:

First hang all tracks with the lowest build order number. Then, continue in the same manner for the next build order group until all groups have been placed.

The receiving prongs for the slinky are quite brittle. Take care to keep them intact while you are hanging tracks in the installation.

Take a single track from the lowest remaining build group, preferably following the order designated in the track list document. Loosen the rope knots that are used to tie the track segments together, and unpack the track segments from each other. Check the clips attached to the ends of the ropes, find the matching clips on the steel wires, and hang s-hooks at the places where rope holds should connect.

Read the labels on the segments and visualise where the track should be placed, then pick up the track with at least two persons, and place it in the installation. Work your way from the origin terminal, connecting the track to the origin terminal, then connecting all rope holds starting at the origin, until you place the last track segment in the receiving terminal. The last track segment contains a little guide on the track underside that should hook the reception part in the terminal. Check that the rope holds are at approximately the right height, and adjust them, by sliding the knots along the rope, if necessary.

Repeat until all tracks are in place. You may need to adjust rope holds for other tracks when hanging a new track. Make sure to leave all clips in place until all tracks are in place and properly adjusted.

When all tracks are in place, adjust all rope hold heights so that all tracks can successfully be routed. To do this, start at the first slot of the first terminal, and route a ball through the opening. Ensure that the ball successfully completes its journey, adjusting the requisite rope holds until it does. Continue with the next slot until all tracks are completed successfully. Then, route all tracks again, to ensure that all tracks can still be routed after previous adjustments.

When you are 100% sure all tracks can be routed, remove all clips from both the ropes and steel wires, and place them in order in their respective boxes (white boxes, labeled, IKEA Bevara).

Congrats! The installation is now mechanically complete. Proceed with testing to uncover the unavoidable technical issues.

## Integration testing

For integration testing, follow the Start-up and shutdown guide. Use the Troubleshooting Guide to identify any issues and solve them.

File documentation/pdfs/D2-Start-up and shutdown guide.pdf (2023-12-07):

# Start-up and shutdown guide

This guide will give instructions on how Packet Run should be started at the beginning of a day, and how it should be shutdown at the end of one. When you run into issues, consult the Troubleshooting Guide (https://bmd-studio.atlassian.net/wiki/spaces/D2/pages/2192015374) , which lists common issues and how to resolve them.

## Starting up Packet Run

1. Power the installation.
Connect the power plug from the desk to a power source, probably located in the desk as well. All terminals and the Mac mini should boot automatically.
2. Ensure that all terminals have booted properly.
They should be displaying their regular terminal screen (the grey one).
3. Ensure all NFC scanners are working.
Take a ball, and place them on the scanner for each terminal. The screen should display “Invalid packet detected” when the ball is placed on the scanner.
4. Ensure the installation is working.
Make two full runs throughout the installation to ensure the installation is working as expected.

## Shutting down Packet Run

1. Shut down the Mac Mini
a. Switch terminal 1 to the Mac mini by pressing the button behind the top right corner of the screen.
b. In macOS, press Fn-Control-F2 until the Apple icon in the top left corner light up.
c. Press space bar to open the system menu.
d. Navigate down to “Shut down…“ and press enter
e. Press enter again to confirm shutdown
f. Wait for the Mac mini to be shutdown, approximately 15 seconds
2. Disconnect power from the installation
Find the plug connected to the power strip inside the desk and disconnect it from the plug powering it. Go ahead. Do it. The Raspberry Pis will be fine. You got this.
Version | Date | Comment
Current Version (https://bmd-studio.atlassian.net/wiki/display/D2/viewpage.action?pageId=2192179216) (v. 2) | 16 Oct, 2023 13:42 | Lei Nelissen (https://bmd-studio.atlassian.net/wiki/people/5e907ccfe053b30b7aae6a82?ref=confluence)
v. 1 (https://bmd-studio.atlassian.net/wiki/display/D2/viewpage.action?pageId=2198175778) | 03 Oct, 2023 13:43 | Lei Nelissen (https://bmd-studio.atlassian.net/wiki/people/5e907ccfe053b30b7aae6a82?ref=confluence)

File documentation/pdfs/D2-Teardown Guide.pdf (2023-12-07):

# Teardown Guide

This guide describes how the Packet Run installation should be torn down. Please refer to the following documents providing information on track layout, required parts, tools and materials.

Inventory of Parts (https://bmd-studio.atlassian.net/wiki/spaces/D2/pages/2197422088) | Required tools and materials (https://bmd-studio.atlassian.net/wiki/spaces/D2/pages/2197389317) | Track list and build order (https://bmd-studio.atlassian.net/wiki/spaces/D2/pages/2193784833)

## Deconstruction

Deconstructing the installation should be done in the following order, as some parts may not be properly accessible until other parts are removed first.

Removing the desk

Firstly, remove any and all cables that connect the desk to the installation. Remove the ethernet cables from the router (leave them on the ground for now). Also remove both ethernet cables that are directly plugged in to the Mac mini. Store the ethernet cable that has the dongle attached to it in the desk. Remove the power cord that powers the installation from the socket and coil it up on the inside of the desk. Lastly, remove the power cable coming in from terminal 11 from the power socket inside the desk.

Secondly, disconnect both tracks that are attached to the desk. The one under the desk should be freely floating, so you can remove it and put it on the ground for later removal. The outgoing track is bolted to the desk, and you will need to disconnect it in order to remove the desk. Remove the bolts in the track using an M3 Allan wrench. After removing the track, make sure to screw the bolts back in the mount, so that we don’t lose them.

Lastly, keep the peripherals in place using painter’s tape. This goes particularly for the keyboard. If you see mouse dangling somewhere, store in on the inside of the desk. Also, remove the Mac mini from the inside of the desk, after disconnecting all cables.

That’s it. The desk should now be freely movable and can be put to the side. Make sure it is out of the way for now. When moving the desk, take care to lift it using the lower plate of the worktop, as the upper one is not bolted to the rest of the desk.

Dismantling the tracks

The tracks form an intricate web that is difficult to construct. Hence, please take care following the steps carefully and one-by-one, so that reconstructing the tracks is a feasible task.

Firstly, find the box of numbered pairs of IKEA clips. Then, attach a pair of clips to each rope and the corresponding steel cable it is attached to. Try to attach the clip on the steel cable as close as possible to the position where the rope is attach to the steel cable. Ensure the numbers on the clip are matching and don’t disconnect any ropes until all of them have a clip on them.

Afterwards, all tracks should be removed one-by-one. It’s best to remove them in the order they were installed in. Refer to the attached T rack list and build order (https://bmd-studio.atlassian.net/wiki/spaces/D2/pages/2193784833) for the installation order. Remove the tracks with build order number 3 first, then 2 and lastly 1. For removing a single track, follow the next paragaph. Always remove a track with at least two persons.

Firstly, one by one, remove the ropes from the hooks attached to the steel cables. Bunch up the ropes and put them inside of the track. Ensure that the rope hold is attached to the track. If it is not properly attached, use a piece of painter’s tape to make sure it stays in the exact same place when being moved. Leave the hooks hanging on the steel cable for now.

The receiving prongs for the slinky are quite brittle. Please take care when removing tracks and bunching them up that they don’t break.

Track segments should never be disconnected. They should be transported as one single piece.

Secondly, manoeuvre the track out of the installation. This might entail making some weird twister moves in order to get it out in a single piece. The start of the track is locked into a terminal by friction fit. You can remove it by lifting the end of the first segment into the air and wiggling the track out.

Thirdly, pack up the tracks segments in a single package using the rope. Make sure that it’s safe for transportation, paying special attention to the prongs on the receiving slinky piece. Also, ensure that the tracks are sorted into their respective build order groups.

Rinse and repeat until all tracks are removed from the installation.

Removing the terminals

As soon as all tracks have been disconnected from the terminals, the terminals can be removed from the installation as well. Before starting to remove individual terminals, cut all tie-wraps connecting ethernet and power cables to the superstructure.

Firstly, remove the white power cords from each power strip. These cords connect the terminal’s power through to each other. Coil up the power cord belonging to a terminal and put it on one of the hooks for the outgoing tracks.

Secondly, coil up the ethernet cable going to the terminal, and place it on another hook for one of the incoming tracks. Don’t add the coil to the existing coil on the underside of the screen, as the cable lengths have been closely calibrated.

Now that the terminal is fully disconnected, you can remove it from the circle. Terminals should always be transported fully assembled.

Dismantling the superstructure

The superstructure consists of a centre piece, to which three side beams are connected. At the end of these horizontal beams are side plates, to which vertical beams are attached. The assembly of a sidebeam, a vertical beam and two side plates is called a leg.

Firstly, remove all stainless steel cables and support beams. Remove the cables by relaxing the wire strainer and removing the cables from the hooks. Remove the beams by using an Allan key to loosen the center connector piece.

Secondly, position the two lifting tripods on other ends of the steel center piece. Attach the U-shape attachments to the tops of the tripods. Then, lift the tripods so that their tops are slightly above the superstructure. Put the two steel profile pieces in the U-holds over the steel center piece.

Thirdly, unscrew the ring from the underside of the steel center piece, and attach it to the top side of the steel center piece. You can now fit a steel cable around the steel profile pieces and attach it to the ring that is now on top of the steel center pieces. You should end up with a situation where, when the lifting tripods are elevated, the steel center piece is pulled up through the ring.

Fourthly, gently lift elevate the two lifting tripods until one leg is lifted from the ground. Now, all legs should be disassembled from the superstructure one by one. The center piece should remain elevated in the center until all legs are removed. For removing each leg, see the following instructions:

Put the support rod under the leg near the steel side plates, and ensure that it well supports the weight of the leg. Now, loosen the bolts for the vertical beam, and remove the vertical beam from the leg assembly. Then, one-by-one, loosen the bolts connecting the side plate to the horizontal beams and remove the plate from the leg assembly. Finally, remove the support rod so that the weight is returned to the lifting tripods.

Rinse and repeat for the two remaining legs until all side plates and vertical beams are removed. Then, lower the remaining assembly using the lifting tripods, as low as they can go. You can now remove the vertical pieces from the center piece by loosening the bolts and pulling the beam out. Finally, lift the center piece out of the lifting tripods by hand. Try to do this with at least three people.

The superstructure is now fully disassembled and ready for transportation.

Version | Date | Comment

The superstructure is heavy and dangerous. It must be assembled / disassembled by a team of at least four people.

Current Version (https://bmd-studio.atlassian.net/wiki/display/D2/viewpage.action?pageId=2191917061) (v. 8) | 16 Oct, 2023 11:35 | Lei Nelissen (https://bmd-studio.atlassian.net/wiki/people/5e907ccfe053b30b7aae6a82?ref=confluence)
v. 7 (https://bmd-studio.atlassian.net/wiki/display/D2/viewpage.action?pageId=2197553206) | 16 Oct, 2023 10:05 | Lei Nelissen (https://bmd-studio.atlassian.net/wiki/people/5e907ccfe053b30b7aae6a82?ref=confluence)
v. 6 (https://bmd-studio.atlassian.net/wiki/display/D2/viewpage.action?pageId=2197651458) | 09 Oct, 2023 21:57 | Lei Nelissen (https://bmd-studio.atlassian.net/wiki/people/5e907ccfe053b30b7aae6a82?ref=confluence)
v. 5 (https://bmd-studio.atlassian.net/wiki/display/D2/viewpage.action?pageId=2194636844) | 09 Oct, 2023 15:58 | Lei Nelissen (https://bmd-studio.atlassian.net/wiki/people/5e907ccfe053b30b7aae6a82?ref=confluence)
v. 4 (https://bmd-studio.atlassian.net/wiki/display/D2/viewpage.action?pageId=2193817649) | 09 Oct, 2023 15:52 | Lei Nelissen (https://bmd-studio.atlassian.net/wiki/people/5e907ccfe053b30b7aae6a82?ref=confluence)
v. 3 (https://bmd-studio.atlassian.net/wiki/display/D2/viewpage.action?pageId=2194341940) | 09 Oct, 2023 14:36 | Lei Nelissen (https://bmd-studio.atlassian.net/wiki/people/5e907ccfe053b30b7aae6a82?ref=confluence)
v. 2 (https://bmd-studio.atlassian.net/wiki/display/D2/viewpage.action?pageId=2194341927) | 09 Oct, 2023 12:01 | Lei Nelissen (https://bmd-studio.atlassian.net/wiki/people/5e907ccfe053b30b7aae6a82?ref=confluence)
v. 1 (https://bmd-studio.atlassian.net/wiki/display/D2/viewpage.action?pageId=2194178059) | 03 Oct, 2023 13:43 | Lei Nelissen (https://bmd-studio.atlassian.net/wiki/people/5e907ccfe053b30b7aae6a82?ref=confluence)

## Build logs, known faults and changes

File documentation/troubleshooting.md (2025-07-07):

# D2-Troubleshooting Guide

## PACKET RUN

This guide intends to help solve commonly occurring issues while setting up, starting and operating Packet Run. It contains a set of questions and answers that should help achieve this goal.

If even one terminal is broken, the installation cannot work, as almost all paths need all terminals in order to function. When this happens during opening hours, gently inform visiting public that the installation is out of order and attempt to solve the issue.

The Packet Run software can be remotely debugged and updated by Lei. In order for this to work, the installation will need to remain powered. If any of the issues requires escalation, leave the installation powered on, so Lei can take a look later.

## One or more terminals have black screens

Sometimes during boot, the screens don't recognise the Raspberry Pi coming online. Alternatively, some screens might accidentally have a timer set that power off the screen after a set time (often 4 h).

To power up the screen, click the power button that is at the backside of the screen in the bottom right corner. The screen should automatically power on and the terminal screen should show.

Take a note of which screen required pressing the power button so we may fix its settings later.

## All of the terminals are showing a terminal window instead of the regular screen.

This probably means that the clients (terminals) have an issue connecting to the server.

First, verify that the server has booted by peering through the underside of the desk and seeing if the lights are on. The server ifars located on the inside of the desk (on the far side related to the installation).

Secondly, verify that the ethernet switch is powered. It's located on the installation side, on the ouside of the desk. All terminals are connected in order (1-12) and receive internet via the server, which is connected on port 16. Ports 1-12 and port 16 should all be lighted up on the switch.

Thirdly, verify that the Mac mini has two ethernet cables that are connected properly. One (the one in the regular ethernet port) should be connected to an outside internet connection. The other (the one in the USB-C Ethernet dongle), should be connected to the ethernet switch. Verify that the port lights up on the ethernet switch. If it does not, switch the cable to another port to verify that it's working.

If none of this fixes the issue, you might be dealing with a networking setup issue. Escalate to Lei and provide them with the steps you've taken to fix the problem. There might be an issue with boot, particularly in restoring the Packet Run database. This needs to be debugged through a VPN connection to the server. 

## The NFC scanner for a single terminal is not working

The NFC scanners are a bit finicky in both setup and scanning.

First, double-check that the terminal has had a proper chance to scan the tag. Rotate the ball in lots of directions and see if this solves the issue. Alternatively, take the NFC tag out of the ball and place it directly on the topside of the scanner.

If this doesn't solve the issue, you might be dealing with some sort of setup issue. Reboot the terminal by pulling the USB-C (white) cable from the Raspberry Pi on the right backside of the terminal. Wait a couple seconds, then, put it back again and wait for the terminal to boot. Repeat this process three times until definitively asserting that the scanner is broken.

Finally, this might be a wiring issue. Ensure the pins are connected correctly [according to the documentation](../client/README.md). You can access the Raspberry Pi by pulling the wooden frame holding the NFC scanner towards you (put your thumbs on the two tabs). Ensure that all pins are making proper contact, both on the scanner end and on the Raspberry Pi. Affix with hot glue if necessary.

The NFC scanner is initialized only at boot. When this fails, the software will not attempt to automatically reconnect to the scanner. Hence, after every attempted fix, you will need to reboot the Raspberry Pi by temporarily removing the power cable (USB-C, white).

If you want to rewire the pins, make sure you're comfortable doing so. Double-check everything. If you wire the NFC scanner incorrectly, this will destroy both the Raspberry Pi and the NFC scanner, an expensive and time-consuming swap. Escalate if you're uncomfortable.

If the pins are wired wrong or have come loose, you can make an attempt to fix them. To do so, first disconnect the power. Then, swap the pins into the correct position. Double-check that the pin wiring is right, before reconnecting the power. Have someone else take a look if they're available.

If this doesn't fix the issue, the NFC Scanner itself might be broken. Spares are available, look for the red PN532 NFC Scanner boards. To install these, first solder the included headers to the board. Then, remove the jumper cable from the faulty scanner and remove the screws. Then, put the new board in the exact same place and reseat the jumper cables in the same place. Check the [jumper wires documentation](../client/README.md) to ensure they are connected in the right order. Boot the terminal and test.

## One or more terminals are throwing errors

If terminals are briefly disconnected from their ethernet connection, they might end up not automatically reconnecting to the server (they should be). In this case, it might be wise to reset that single terminal and/or all terminals.

To reset a single terminal, find the Raspberry Pi at the backside of the terminal, approximately behind the scanner. Disconnect the white USB-C cable that powers it, wait a few seconds, and then reconnect the cable. The terminal should boot up automatically.

To reset all terminals, find the plug from terminal 11 that is in the power strip on the underside of the desk. It should be white. Remove it from the power strip, wait a few seconds, then plug it in again. All terminals should boot up automatically. Then, press F5 on both terminals with a keyboard to reset these as well.

## The press is not working

The press works because there is a small magnet in the press, and a small hall sensor right next to the NFC scanner. First, verify that the hall sensor is still working by placing a magnet on flat piece of 3D-printed material, on the left of the NFC scanner. If this doesn't work, you'll need to replace the sensor itself.

To replace the sensor, pull the wooden part in which the NFC-scanner is seated towards you by pushing your thumbs on the two tabs. Then, remove the hall sensor from the scanner module with the help of some plyers. 

If no readymade hall sensor assembly is available, you'll need to make your own. Take one of the jumper cables with the purple wires, and strip them bare on one end. Then, place some heatshrink tubing, before soldering to the legs of an available hall sensor component. Check the [jumper wires documentation](../client/README.md) for the best way to connect them, but the prevailing wisdom is black = ground, white = supply, purple = signal. 

With the complete hall sensor assembly, bend the sensor itself 90 degrees, so that the flat side of the component (the non-branded side) is oriented outwards. This is the side of the component that needs to be oriented towards the magnet. Push it down in the hall sensor cavity so that it's as far as it can go. Use hot glue to affix the component. Connect the cables to the Raspberry Pi and test whether it works again.

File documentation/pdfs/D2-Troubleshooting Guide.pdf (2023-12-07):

# Troubleshooting Guide

This guide intends to help solve commonly occurring issues while setting up, starting and operating Packet Run. It contains a set of questions and answers that should help achieve this goal.

When running into issues during operation, and you cannot use this guide to resolve these issues, first contact your shift responsible. Then, escalate to preferably Lei (+31 6 420 300 98) or alternatively Jort (+31 6 434 314 93).

If even one terminal is broken, the installation cannot work, as almost all paths need all terminals in order to function. When this happens during opening hours, gently inform visiting public that the installation is out of order and attempt to solve the issue.

️ One or more terminals have black screens

Sometimes during boot, the screens don’t recognise the Raspberry Pi coming offline. Alternatively, some screens might accidentally have a timer set that power off the screen after a set time (often 4h).

To power up the screen, click the power button that is at the backside of the screen in the bottom right corner. The screen should automatically power on and the terminal screen should show.

Take a note of which screen required pressing the power button so we may fix its settings later.

📠 All of the terminals are showing a terminal window instead of the regular screen.

This probably means that the Raspberry Pis have an issue connecting to the server (the Mac mini).

First, verify that the Mac mini has booted by peering through the underside of the desk and seeing if the front light indicator is on. It faces the side of the desk and should be white. If it’s off, push the power button on the backside (black side) of the Mac mini and wait for the terminals to show the terminal screens automatically.

Secondly, verify that the ethernet switch is powered. Check that there are lights on the ethernet switch that is integrated in the side of the desk.

Thirdly, verify that the Mac mini has two ethernet cables that are connected properly. One (the one in the regular ethernet port) should be connected to an outside internet connection. The other (the one in the USB-C Ethernet dongle), should be connected to the ethernet switch. Verify that the port lights up on the ethernet switch. If it does not, switch the cable to another port to verify that it’s working.

If none of this fixes the issue, you might be dealing with a networking setup issue. Escalate to Lei or Jort and provide them with the steps you’ve taken to fix the problem.

📡 The NFC scanner for a single terminal is not working

The NFC scanners are a bit finicky in both setup and scanning.

First, double-check that the terminal has had a proper chance to scan the tag. Rotate the ball in lots of directions and see if this solves the issue. Alternatively, take the NFC tag out of the ball and place it directly on the topside of the scanner.

If this doesn’t solve the issue, you might be dealing with some sort of setup issue. Reboot the terminal by pulling the USB-C (white) cable from the Raspberry Pi on the right backside of the terminal. Wait a couple seconds, then, put it back again and wait for the terminal to boot. Repeat this process three times until definitively asserting that the scanner is broken.

Finally, this might be a wiring issue. Ensure the pins are connected correctly according to the documentation: https://gitlab.moeilijkedingen.nl/ddw-2023/packet-run/-/tree/main/client. You can access the Raspberry Pi by pulling the wooden frame holding the NFC scanner towards you. Ensure that all pins are making proper contact, both on the scanner end and on the Raspberry Pi.

If the pins are wired wrong or have come loose, you can make an attempt to fix them. To do so, first disconnect the power. Then, swap the pins into the correct position. Double-check that the pin wiring is right, before reconnecting the power. Have someone else take a look if they’re available.

If this doesn’t fix the issue, the NFC Scanner itself might be broken. We have spares available. Escalate to Lei or Jort to get those fixed.

⛔️ One or more terminals are throwing errors

If terminals are briefly disconnected from their ethernet connection, they might end up not automatically reconnecting to the server (they should be). In this case, it might be wise to reset that single terminal and/or all terminals.

To reset a single terminal, find the Raspberry Pi at the backside of the terminal, approximately behind the scanner. Disconnect the white USB-C cable that powers it, wait a few seconds, and then reconnect the cable. The terminal should boot up automatically.

To reset all terminals, find the plug from terminal 11 that is in the power strip on the underside of the desk. It should be white. Remove it from the power strip, wait a few seconds, then plug it in again. All terminals should boot up automatically. Then, press F5 on both terminals with a keyboard to reset these as well.

📟 One terminal is stuck in a weird state

Sometimes, people might do a weird run and a terminal might be stuck in a state it can’t get out of. You can reset terminal state through the Mac mini.

To reset the state, switch terminal 1 to the Mac mini by pressing the button that is at the backside of the monitor in the right top corner. If macOS does not automatically show up, press the monitor power button at the backside in the right bottom corner. If it shows white snow, press the button at the right top corner two more times slowly. Also, retrieve the mouse that is stored on the underside of the desk (left side).

A Chrome window should already be open showing all terminals. If there isn’t open a Chrome window and navigate to http://localhost:3000. Click the terminal that is stuck, and in the pop-up screen in the left top corner, click “Reset terminal”.

️ None of the maps are displaying / ❓ Terminal addresses are always “???” / ⌨️ Terminal 1 never allows a website typed in

It appears that the internet connection might be acting up.

Ensure that the cable that connects to the Ethernet port on the Mac mini is connected correctly.

Double-check that the Mac mini has a connection to the internet. Switch terminal 1 to the Mac mini by pressing the button that is at the backside of the monitor in the right top corner. If macOS does not automatically show up, press the monitor power button at the backside in the right bottom corner. If it shows white snow, press the button at the right top corner two more times slowly. Also, retrieve the mouse that is stored on the underside of the desk (left side).

Then, navigate to Google, and check if the website is loading and working as expected. With this information, escalate to Lei or Jort.

Version | Date | Comment

The NFC scanner is initialized only at boot. When this fails, the software will not attempt to automatically reconnect to the scanner. Hence, after every attempted fix, you will need to reboot the Raspberry Pi by temporarily removing the power cable (USB-C, white).

If you want to rewire the pins, make sure you’re comfortable doing so. Double-check everything. If you wire the NFC scanner incorrectly, this will destroy both the Raspberry Pi and the NFC scanner, an expensive and time-consuming swap. Escalate if you’re uncomfortable.

Current Version (https://bmd-studio.atlassian.net/wiki/display/D2/viewpage.action?pageId=2192015374) (v. 2) | 16 Oct, 2023 14:28 | Lei Nelissen (https://bmd-studio.atlassian.net/wiki/people/5e907ccfe053b30b7aae6a82?ref=confluence) v. 1 | 03 Oct, 2023 13:44 | Lei Nelissen

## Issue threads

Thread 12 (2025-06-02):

Fixatie terminals voor afscherming knikkerbaan & vastzetten terminals op positie

bvandijk, 2025-06-02:
De terminals kunnen onderling verschuiven, dit beinvloed hoe de banen lopen. Terminals moeten vast zitten op eigen plaats. Daarnaast kan deze fixatie zorgen voor afscherming van de knikkerbaan zodat bezoekers niet tussen de banen (met alle gevolgen van dien) gaan lopen.

bvandijk, 2025-06-09:
Lei komt woensdag met uitsluitsel over tape op vloer

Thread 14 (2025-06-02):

More feedforward voor het begin.

jortbmd, 2025-06-02:
Tijdens het begin scherm is het wenselijk om meer feedforward te geven. Als in:
- Why
- What
- How
- Who

Doel is om dingen beter uit te leggen en beter over te brengen wat de installatie inhoudt en wat de bezoeker gaat doen.

Closed 2025-06-20.

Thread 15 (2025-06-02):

Haakjes bovenbalk vervangen om verschuiven te voorkomen.

bvandijk, 2025-06-02:
De touwtjes zitten aan de bovenbalk vast met haakjes welke kunnen verschuiven. Een gevolg hiervan is dat de banen verschuiven. Verkennen hoe deze haakjes kunnen worden vervangen zodat ze vast zitten aan de bovenbalk.

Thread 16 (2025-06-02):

Helder de keuzes voor alternatieve routes presenteren

leinelissen, 2025-06-02:
Zorgen dat specifiek de metrics beter uitgelicht worden, maar niet sleutelen aan de metrics of aan de informatie om een keuze te maken (dat is een andere issue).

Closed 2025-06-24.

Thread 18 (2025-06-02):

Mechanisch: Bakjes en hendel verbeteren

jortbmd, 2025-06-02:
De bakjes en hendels zijn niet altijd even stevig. Vooral de bakjes vallen er af en toe onderuit. Deze moeten aangepast worden zodat dit niet meer gebeurd.

Closed 2025-06-23.

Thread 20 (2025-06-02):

Animatie voor inpakken / uitpakken packet

leinelissen, 2025-06-02:
Een animatie die duidelijk maakt wat er gebeurt met een pakketje zodra je de hendel gebruikt. Laten zien dat er informatie in en uit gaat en wat die data precies doet.

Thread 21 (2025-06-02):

Hufter proof terminals

bvandijk, 2025-06-02:
Hufter proof maken van terminals door het verstevigen van de verbindingen. Sommige friction fit onderdelen zijn eenvoudig los te schuiven. Deze moeten goed worden bevestigd zodat ze niet onbedoeld los kunnen raken. Bij voorkeur geen lijm gebruiken zodat de installatie later gedemonteerd kan worden. Het kan eventueel wel met kleine dotjes.

Closed 2025-07-14.

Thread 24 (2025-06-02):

Toevoegen aparte uitleg bij aankomst

leinelissen, 2025-06-02:
Als je een balletje scant dat terugkomt bij het bureau krijgt je nu direct de website te zien. We willen een scherm toevoegen dat duidelijk dat de data uit het balletje komt en dat dat gebruikt om een website te laten zien, en daarna pas de website zelf laten zien.

Closed 2025-07-14.

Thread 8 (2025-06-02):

Terminal receiving packets - baan (met U-tje) bevestiging op terminal raakt los of schuift door

bvandijk, 2025-06-02:
De baan zit met een Utje met dubbelzijdig tape op de terminal vast. Door verschuiven van de baan kan de baan tegen de terminal aan komen, waardoor de ballen niet uit de baan vallen.

Closed 2025-06-06.

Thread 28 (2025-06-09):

Design voor labeling van de terminals

jortbmd, 2025-06-09:
De labels van de terminals moeten ontworpen worden.
Bart neemt het gat ontwerp opzich. De rest van de ontwerpen voor het aangeven van het scannen en de namen van de terminals moeten nog ontworpen worden.

Closed 2025-07-14.

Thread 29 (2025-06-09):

Start en eindig hier bordjes boven het bureau ontwerpen.

jortbmd, 2025-06-09:
Er moet een bordje komen te hangen die aangeeft waar te starten en eindigen.

In de lengte van het bureau dient iets te hangen wat aangeeft wat het begin en einde is.
Aan de kop van het bureau hebben we een bordje nodigt die aangeeft waar er begonnen dient te worden.

Closed 2025-06-09.

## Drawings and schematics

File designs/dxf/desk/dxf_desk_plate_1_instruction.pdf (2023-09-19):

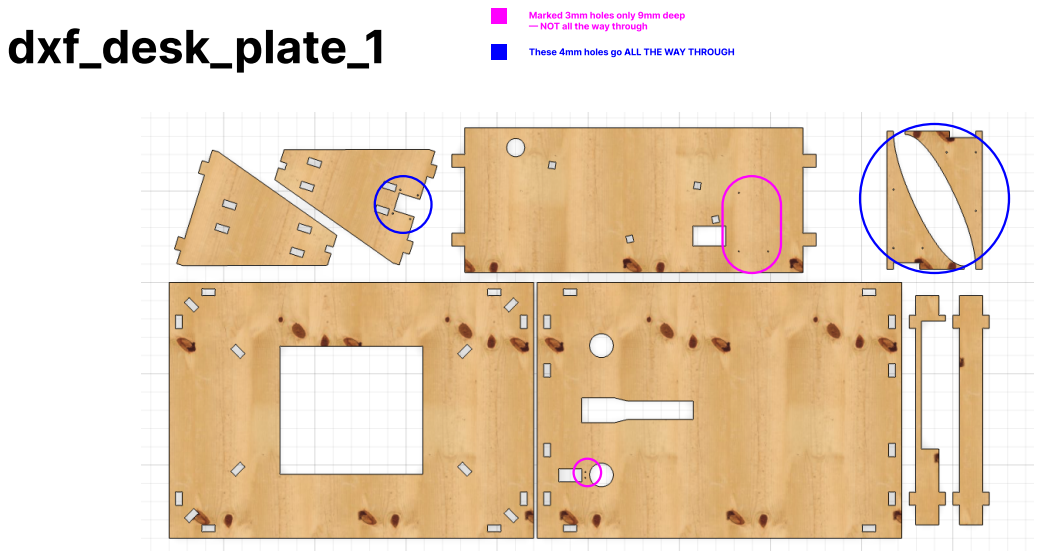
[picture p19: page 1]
–– NOT all the way through dxf_desk_plate_1; These 4mm holes go ALL THE WAY THROUGH

Marked 3mm holes only 9mm deep

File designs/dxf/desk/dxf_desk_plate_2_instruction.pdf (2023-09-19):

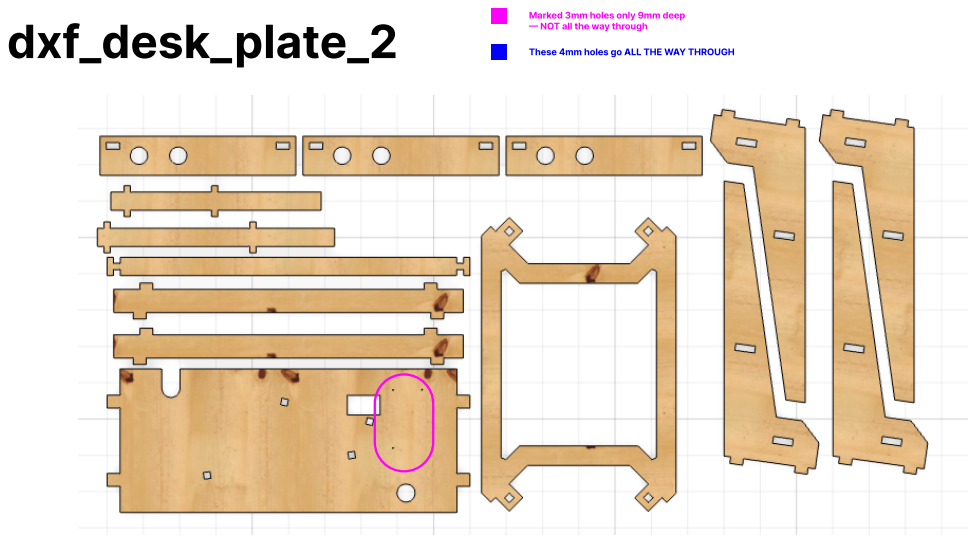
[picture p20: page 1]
–– NOT all the way through dxf_desk_plate_2; These 4mm holes go ALL THE WAY THROUGH

Marked 3mm holes only 9mm deep

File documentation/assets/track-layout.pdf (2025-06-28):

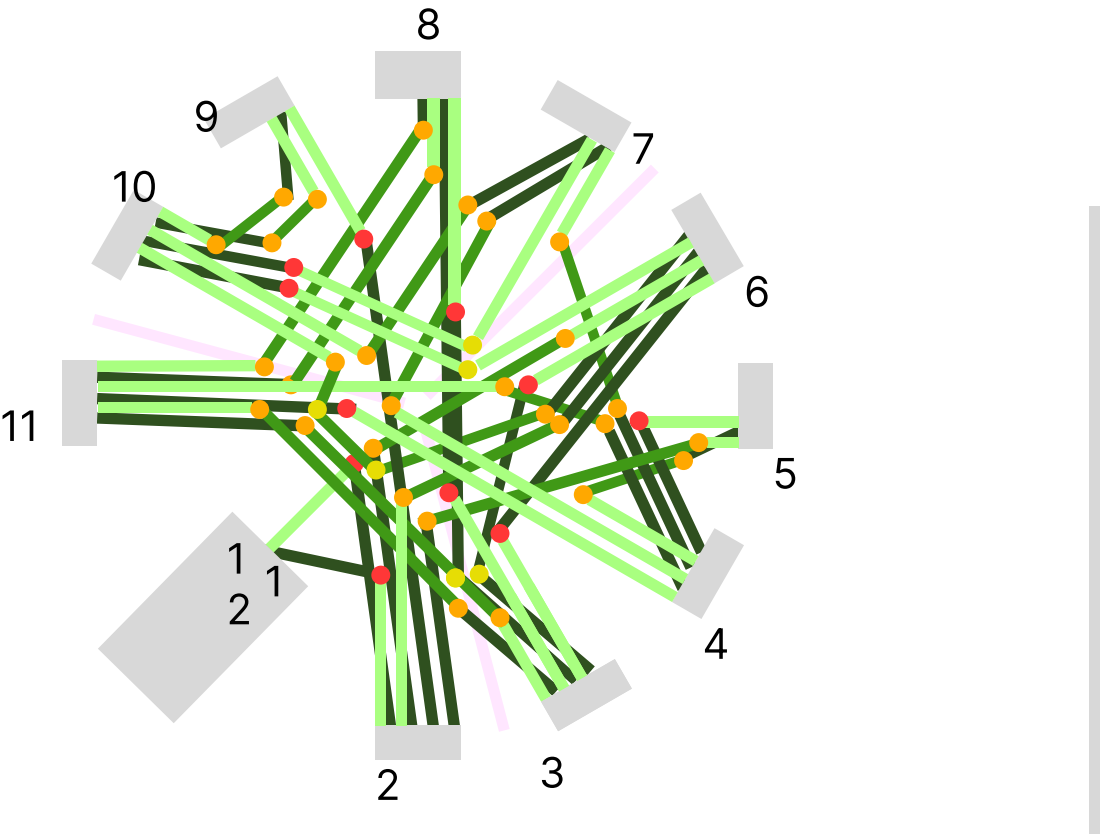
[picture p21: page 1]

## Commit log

2023-08-04 feat: keep track of subscriptions and delete behaviorsubjects when they're not needed anymore
2023-08-11 feat: implement traceroute worker
2023-08-24 fix: order terminals so the slots do not interfere
2023-08-25 feat: also store slot number on the terminal connections
2023-08-25 feat: add computed property for current hops from run
2023-08-25 fix: actually make reset button work
2023-08-29 fix: traceroute destination
2023-08-29 feat: allow scanning packet at current terminal
2023-08-29 fix: terminal slot ordering
2023-08-29 feat: differentiate between future and current hops
2023-08-30 fix: show available hops in correct slots
2023-09-01 feat: add config for rpi devices
    [packet_run_config.txt]
2023-09-18 feat: upload done files
    [rope_hold.stl, terminal.dxf]
2023-09-18 feat: add updated design of arrival and drop
    [arrival.stl, drop.stl]
2023-09-18 feat: add peg for 3d printing
    [peg.stl]
2023-09-19 feat: add drill guide stls
    [drill_guide_body.stl, drill_guide_lid.stl]
2023-09-19 fix: extend drill guide
    [drill_guide_lid.stl]
2023-09-19 feat: add dxf for desk
    [dxf_desk_plate_1.dxf, dxf_desk_plate_2.dxf, dxf_desk_plate_3.dxf]
2023-09-19 feat: add basic hall sensor script
2023-09-19 feat: add log message to hall sensor server
2023-09-19 fix: configure hall sensor as input
2023-09-19 feat: document hall effect sensor
2023-09-19 feat: add hall sensor server to boot script
2023-09-19 fix: run hall sensor script relative to script
2023-09-19 feat: refactor sender flow
2023-09-20 Test print; print time 1h32
    [desk_departure.stl]
2023-09-20 fix: only run hall sensor when necessary on sender
2023-09-21 fix: add step file so Ephi can make a dxf export, for the fusion spline dxf export is broken af
    [curved_slope v9.step]
2023-09-22 Upload New File
    [peg_desk_18.00.stl]
2023-09-22 feat: add first versions for nfc cup and packet press
    [nfc_cup.stl, packet_press.stl]
2023-09-26 STL: added files for scanner, packet press, and containers
    [cup_scanner.stl, grill_handle.stl, grill_hinge_arm.stl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]
2023-09-28 feat: added desk arrival stl
    [desk_arrival.stl]
2023-09-28 chore: updated print list
2023-09-29 fix: replaced desk arrival
    [desk_arrival.stl]
2023-09-29 chore: replaced desk arrival once again. Uploaded the wrong file
    [desk_arrival.stl]
2023-09-29 fix: changed hinge cover to use bolts instead of clickfingers.
    [hinge_container.stl, hinge_container_cover.stl]
2023-10-02 doc: added the SDA en SCL reference for the nfc reader board pinout and connection.
2023-10-03 Re-exported cup to ensure 35mm cutout for hinges
    [nfc_cup.stl]
2023-10-03 feat: add desik arrival stl to repo
    [arrival_desk.stl]
2023-10-03 feat: add final missing parts to repo
    [final_parts.dxf]
2023-10-03 fix: log how the raspberry pi loops through ports
2023-10-03 fix: set CORS on hall sensor server
2023-10-03 fix: log errors when reading hall sensor
2023-10-04 fix: added rib to hold locking nut in place. Minor improvement - previous versions are still ok.
    [grill_hinge_arm.stl]
2023-10-05 fix: remoe outdated desk_arrival stl
    [desk_arrival.stl]
2023-10-05 fix: reverse terminal slots to match reality
2023-10-06 feat: add end hook
    [track_end_hook.stl]
2023-10-06 chore: move alternate pegs to its own folder
    [peg_desk_18.00.stl, peg_desk_18.25.stl, peg_desk_18.50.stl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]
2023-10-07 fix: only highlight map marker for current location
2023-10-07 fix: receiver flow
2023-10-10 fix: swapped slots for server1
2023-10-10 fix: display empty slots when not all slots have hops
2023-10-10 fix: account for unique traceroute constraint
2023-10-11 fix: contain bounds to only current and available hops
2023-10-13 feat: add deskdispenser
    [bottom_part.stl, side_wall.stl]
2025-06-25 feat/fix: updated various 3D parts for 2025 exhibition
    [bottom_wood_clamp.stl, cable_clamp.stl, desk_leg_bracket.stl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]
2025-06-28 feat: first stab at generating pi image
    [generic64-apt-pi4.cfg, packet_run_config.txt]
2025-06-28 feat: rearchitect image gen into layers
    [deb12-arm64.cfg, packet-run-client.cfg, packet-run-server.cfg]
2025-06-28 fix: proper routing for devices on 10.13.37.0./24
2025-06-28 fix: disable console over uart so we can use it for the nfc scanner
2025-06-28 docs: update parts, tools and materials
2025-06-28 docs: add track layout pdf
2025-06-29 feat: Updated styling for the onboarding screens to reflect current UI.
2025-06-29 feat: got the first couple of onboarding screens ready.
2025-06-29 feat: completed onboarding flow according to designs.
    TODO: add image/animation at the end explanation.
    TODO: Test in production
2025-06-29 fix: route markers overlapt the map at the current height. Reduced this.
2025-06-29 chore: Removed the InfoBox and Journey visual as it was not in the current design.
2025-06-29 fix: the route name and destination needed to be switched around. Somehow deleted the name.
2025-06-29 feat: added map including question mark when nog current location is present.
2025-06-29 feat: added end flow.
2025-06-29 feat: update all the onboarding screens to reflect the current design. TODO: Add the packet scanner animation
2025-06-29 fix: added filtering for unknown coordinates. So on the map it does not end up in the middle of the ocean.
2025-07-01 fix: add traceroute package to server
2025-07-02 feat: delay map loading by a couple seconds
2025-07-14 fix: updated grill_hinge_fixed part to integrate the nut and bolt into the part. Fixes collision with container during installation.
    [grill_hinge_fixed.stl]
